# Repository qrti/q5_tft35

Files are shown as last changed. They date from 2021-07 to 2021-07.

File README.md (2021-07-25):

# **FLSUN Q5 3.5" Display**

## A bigger display for the FLSUN Q5

<br>

### Summary
Four brackets at the corners of the control box's display opening are screwed to the existing thread holes. The bracket's arms lead through the opening, holding a Makerbase MKS Robin TFT35 3.5" LCD display at an angle of 15 degrees for convenient operation. A snap-in casing is also included.

<br>

### Print
The brackets should be rotated appropriately to minimize support structures. To produce sturdy parts the infill rate should be at least 25 %. After printing the support material has to be removed, especially the 1.5 mm slits that should fit to the control box opening sheet might need a slight  rework with a warding file.

<br>

### Assembly
The existing 2.4" LCD is removed by unscrewing four fixing screws and unplugging the ribbon cable. To gain some more space for fingers and tools, the power supply's housing might be loosened. The brackets are screwed to the original display's thread holes at the inside of the control box. For easier fastening M3 screws preferable with hexagonal heads can be used. The new LCD is connected to the ribbon cable and its PCB fixed with four M3 screws, washers and nuts to the brackets. The ribbon cable might be relocated to utilize its full length.

<br>

### Marlin configuration.h

version 2.0.9.1  
```
#define MKS_ROBIN_TFT35
#define TFT_ROTATION TFT_ROTATE_180
#define TFT_COLOR_UI
#define TOUCH_SCREEN_CALIBRATION
#define SINGLE_TOUCH_NAVIGATION
#define TOUCH_CALIBRATION_AUTO_SAVE

```

version 2.0.7.2  
```
#define TFT_480x320
#define TFT_ROTATION TFT_ROTATE_180

#define TOUCH_CALIBRATION_X     17191               // these values might do as a starting point, 
#define TOUCH_CALIBRATION_Y     -11709              // the exact values can be found by issuing
#define TOUCH_OFFSET_X          -34                 // marlin M995 command
#define TOUCH_OFFSET_Y          332
#define TOUCH_ORIENTATION       TOUCH_LANDSCAPE
```
<br>

### Files
[-> 3d print](stl)

<br>

### Thingiverse
https://www.thingiverse.com/thing:4909820

<br>

---

<br>

## Views

Display with casing  
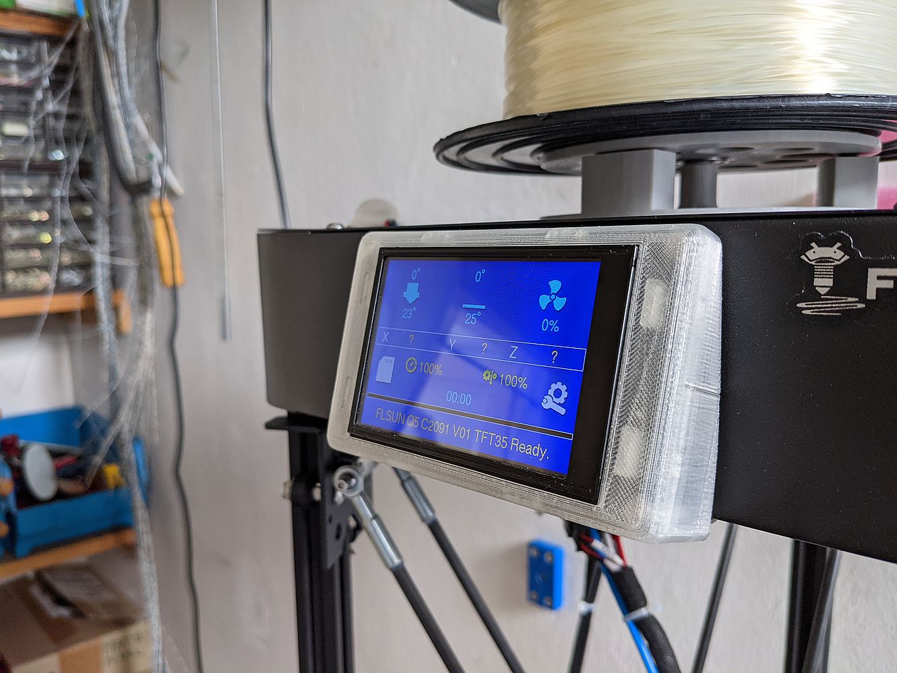
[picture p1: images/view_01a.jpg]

<br>
<br>

Display without casing  
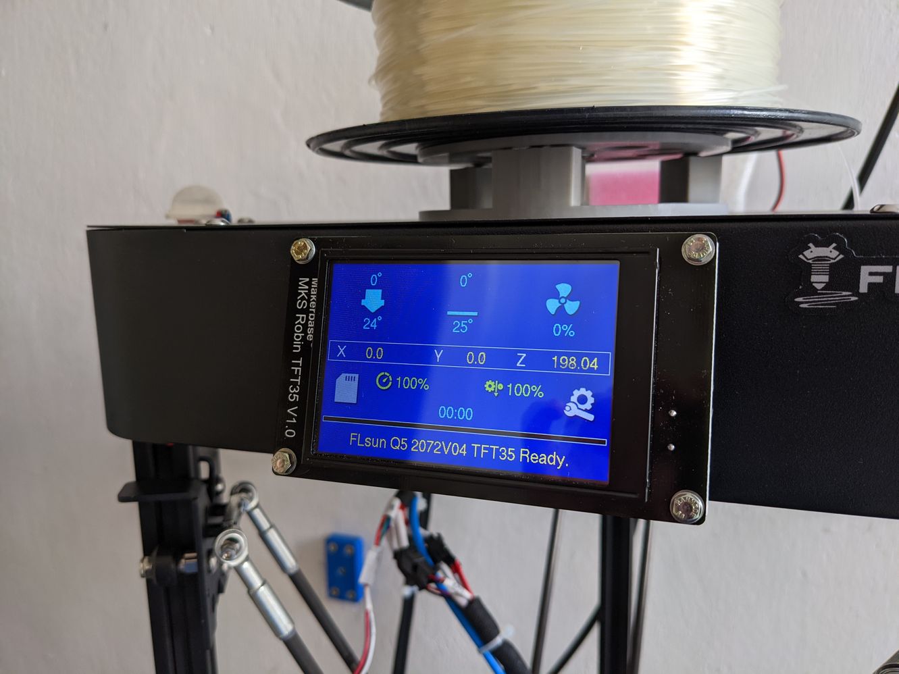
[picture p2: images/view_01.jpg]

<br>
<br>

Side  
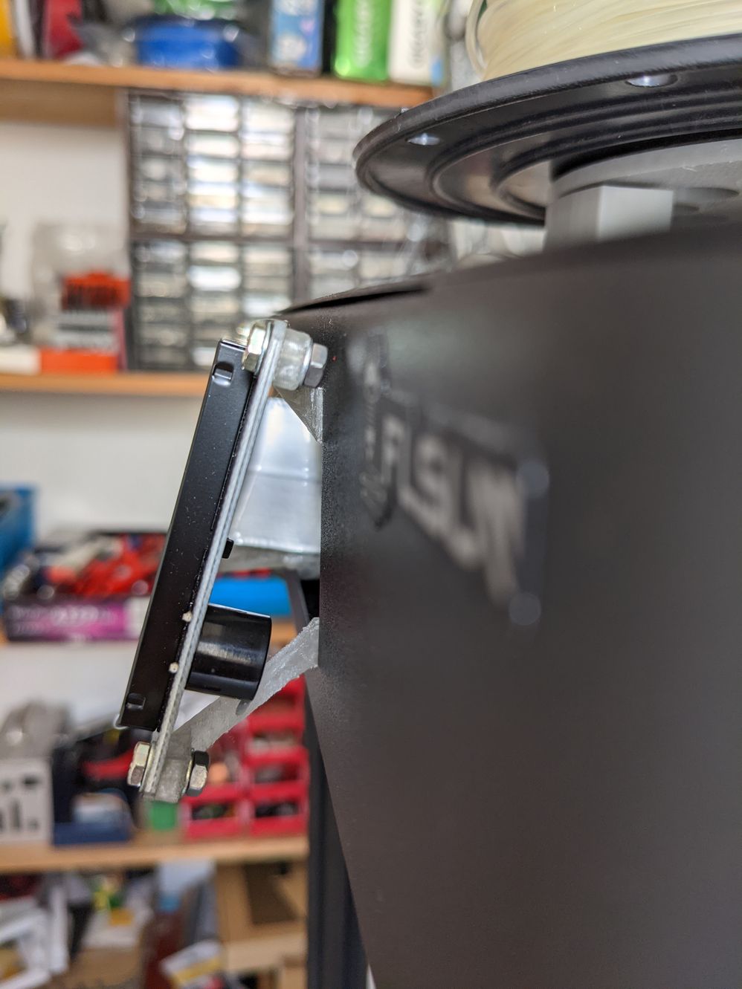
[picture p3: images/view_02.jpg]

<br>
<br>

Bottom  
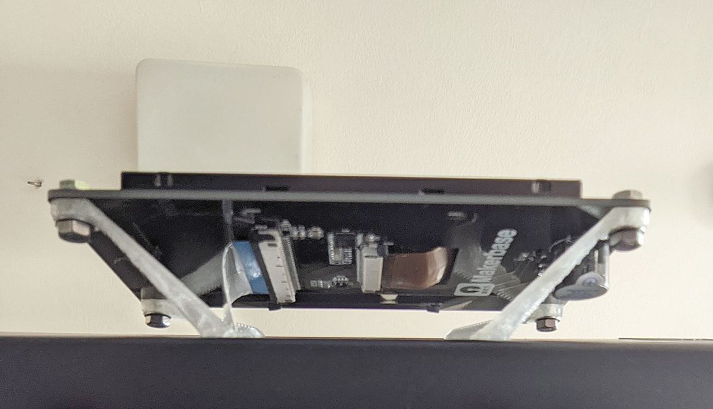
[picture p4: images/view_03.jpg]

<br>
<br>

Control box inside  
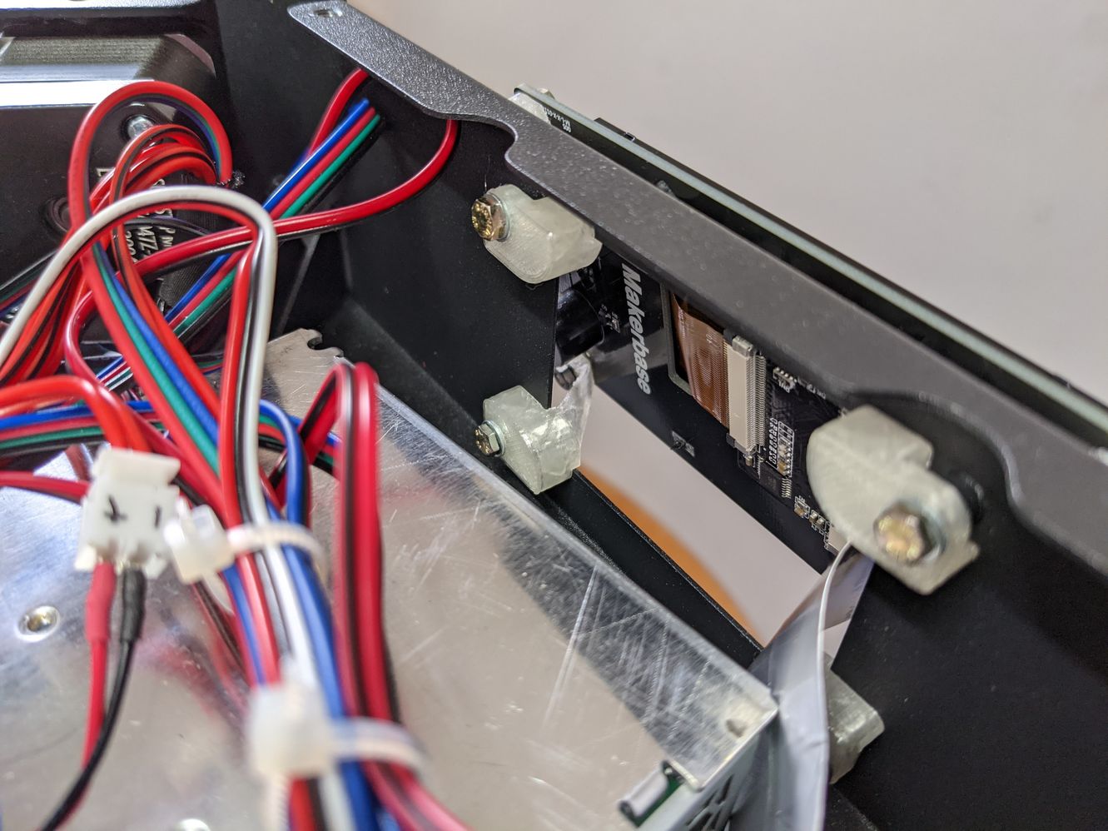
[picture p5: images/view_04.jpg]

<br>
<br>

## Renders

Side with TFT  
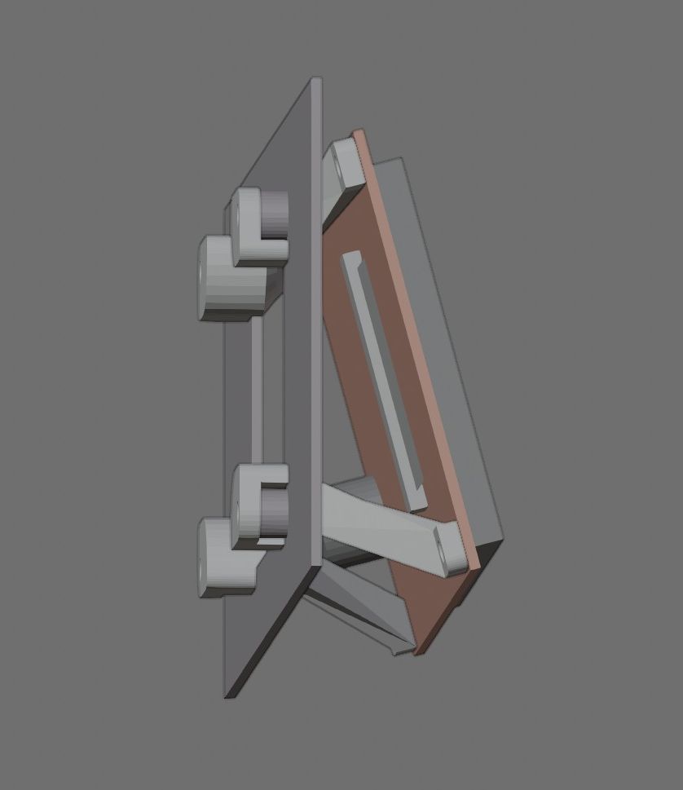
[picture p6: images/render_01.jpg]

<br>
<br>

Front  
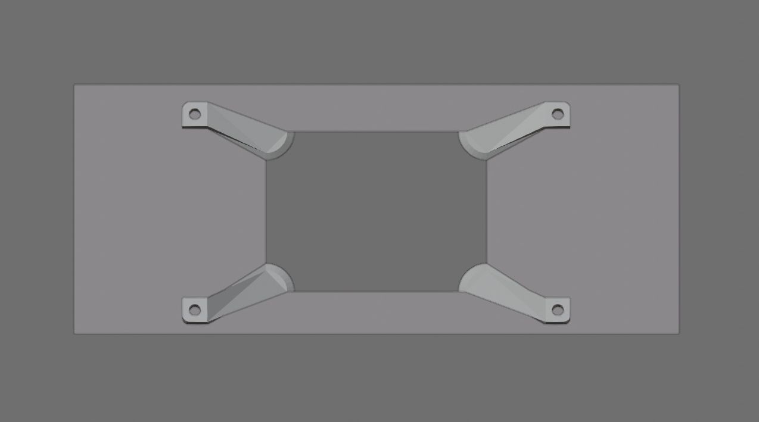
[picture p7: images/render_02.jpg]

<br>
<br>

Top Side  
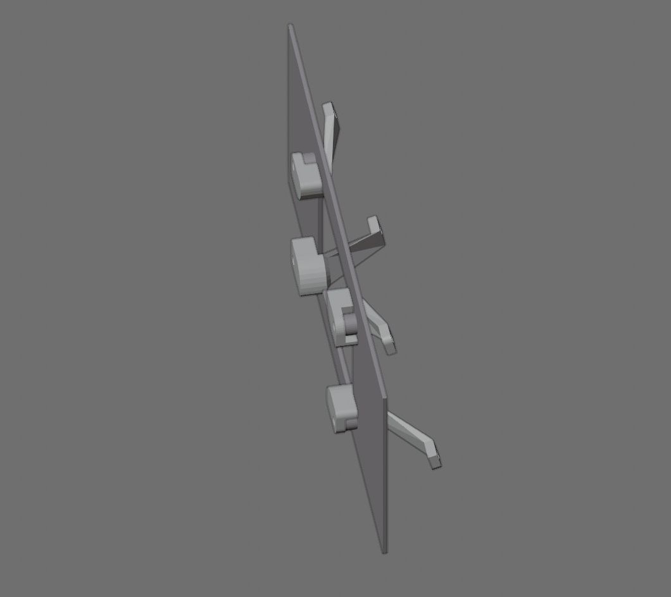
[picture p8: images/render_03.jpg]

<br>
<br>

Top  
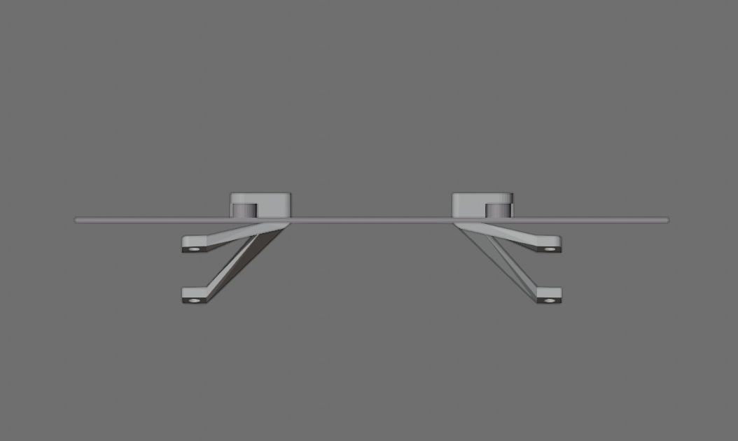
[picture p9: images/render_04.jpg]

<br>
<br>

Snap-in casing  
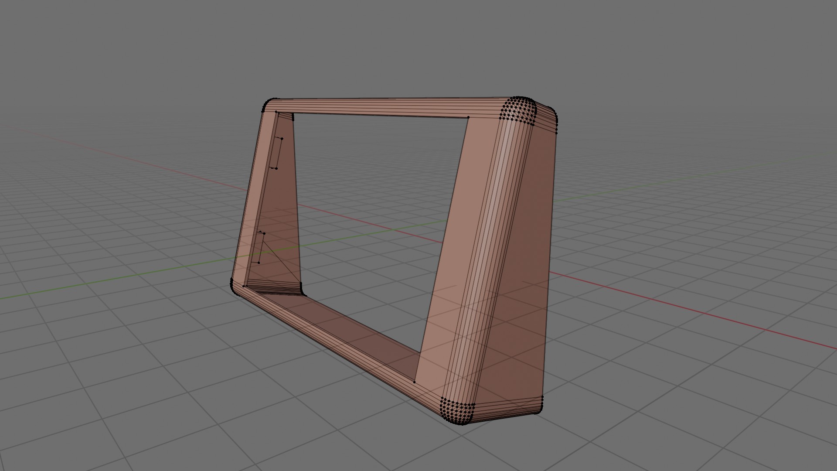
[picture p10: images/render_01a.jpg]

<br>
<br>

<br>
<br>

---

[qrt@qland.de](mailto:qrt@qland.de) 210725

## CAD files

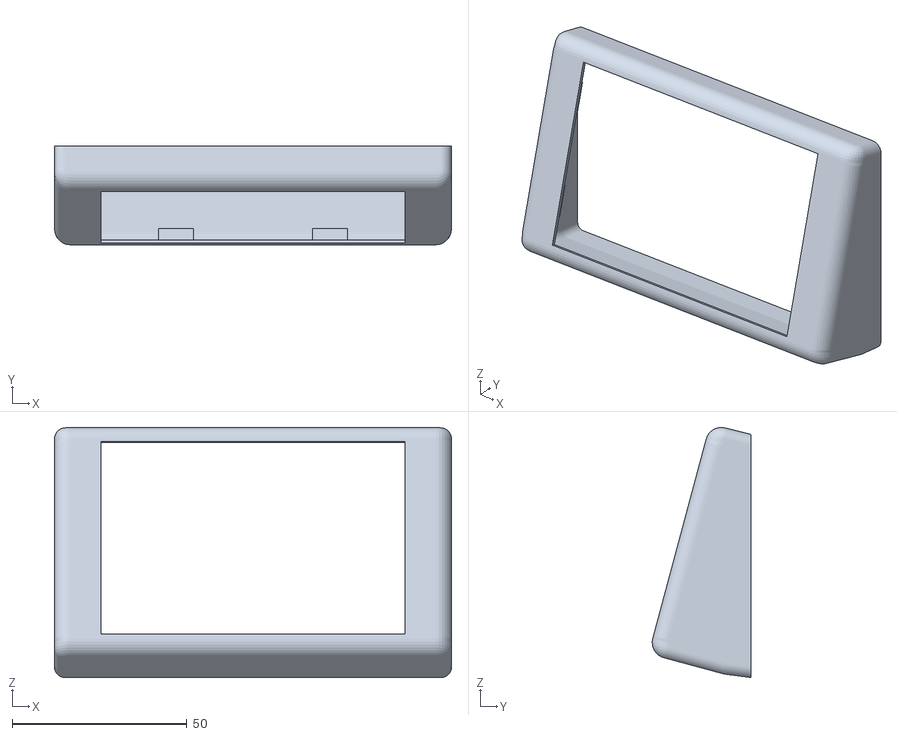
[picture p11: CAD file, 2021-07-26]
stl/q5_display_casing_v2.stl
113.5 x 28.2 x 71.5

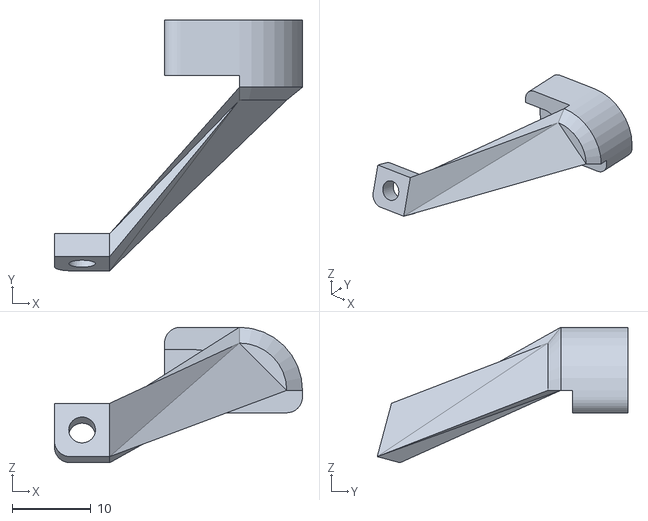
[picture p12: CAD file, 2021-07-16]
stl/q5_display_bracket_bot_left.stl
31.5 x 31.8 x 17.2

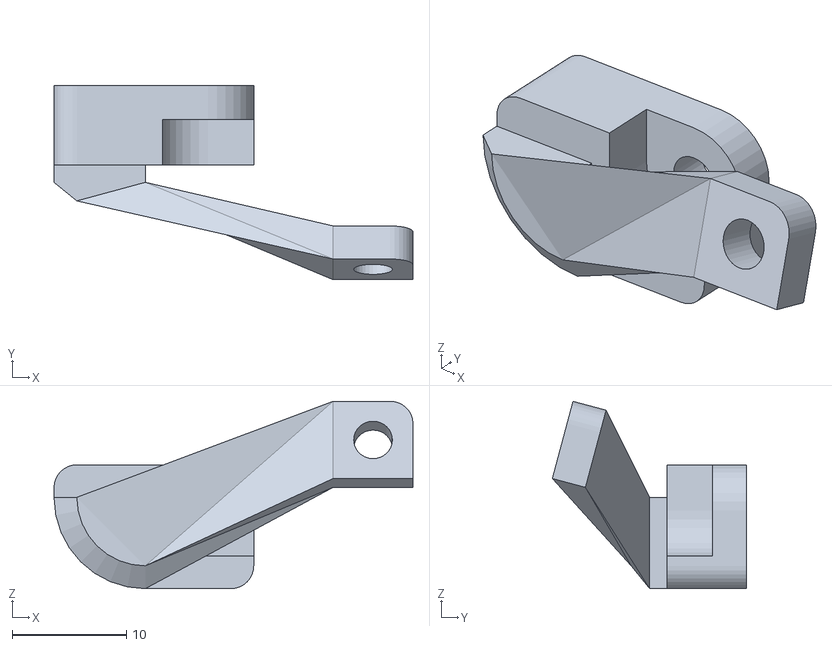
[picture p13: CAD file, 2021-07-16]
stl/q5_display_bracket_top_right.stl
31.5 x 17.0 x 16.4

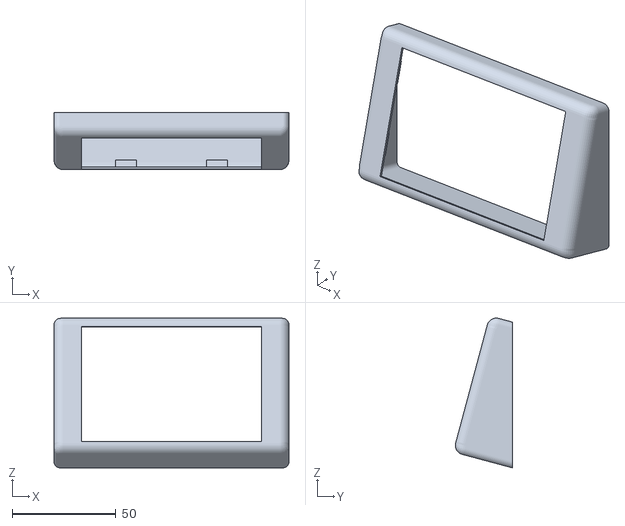
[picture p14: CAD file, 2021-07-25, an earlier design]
stl/q5_display_casing.stl
113.5 x 27.7 x 72.4

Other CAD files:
stl/q5_display_bracket_bot_right.stl
stl/q5_display_bracket_top_left.stl
